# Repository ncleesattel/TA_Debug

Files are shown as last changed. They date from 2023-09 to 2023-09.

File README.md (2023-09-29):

# TA_Debug
PCB designed with KiCad to make a debug main unit for TeenAstro V3 testing.  
I haven't built my own debug platform yet, so I would encourage you to wait for my feedback.  

## internal connectors
The pcb is intended to accommodate:
* TMC5160 for RA, DEC and Focusser
  * the TMC5160 can either be connected via step/dir or SPI 
* 16 MHz oscillators for TMC5160
* NEO-M8n GNSS satellite positioning system
* DS3232 RTC
* power is supplied from a DC jack that splits into
  * VCC for steppers (12 - 24V)
  * 5V for legacy SHC
  * 3.3V for everything else
  * CR32 battery
* power is provided by two Traco DC/DC converters

## external connectors
An MCU like ESP32 or Teensy 4.x can be connected through a ribbon cable to a breadboard.  
There are also connectors for an SHC, stepper motors and encoders.  

## pictures
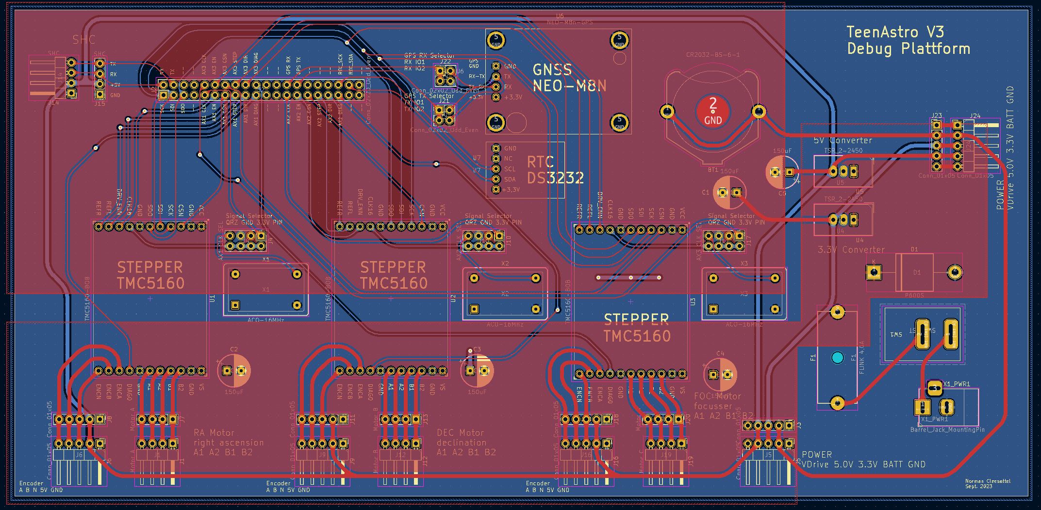
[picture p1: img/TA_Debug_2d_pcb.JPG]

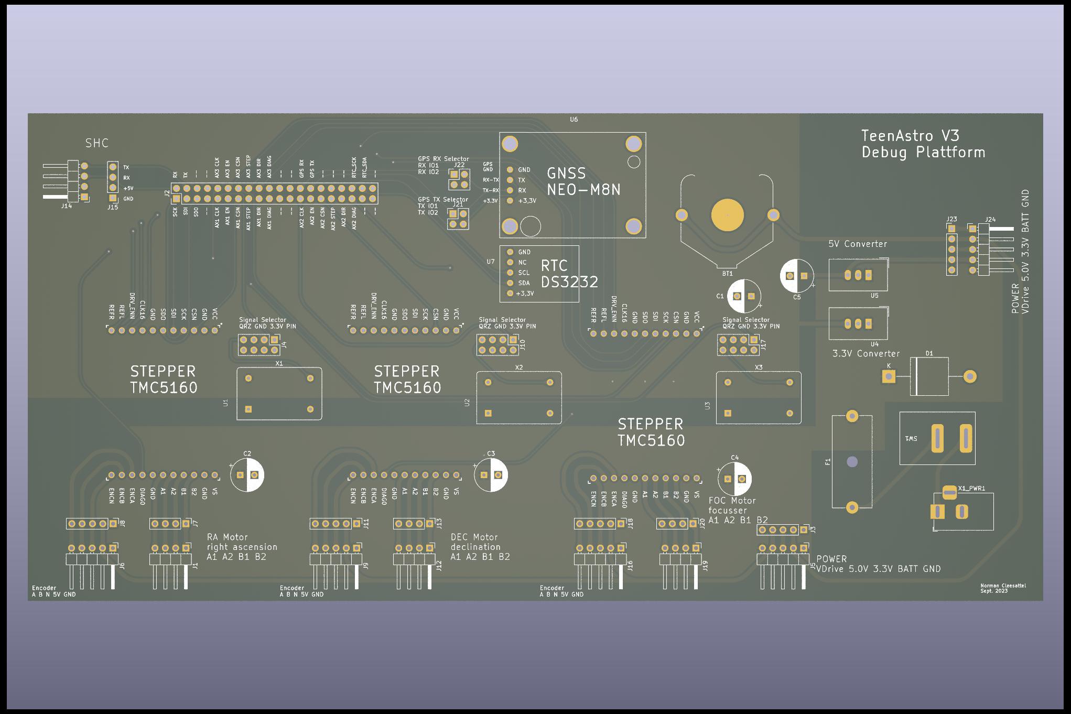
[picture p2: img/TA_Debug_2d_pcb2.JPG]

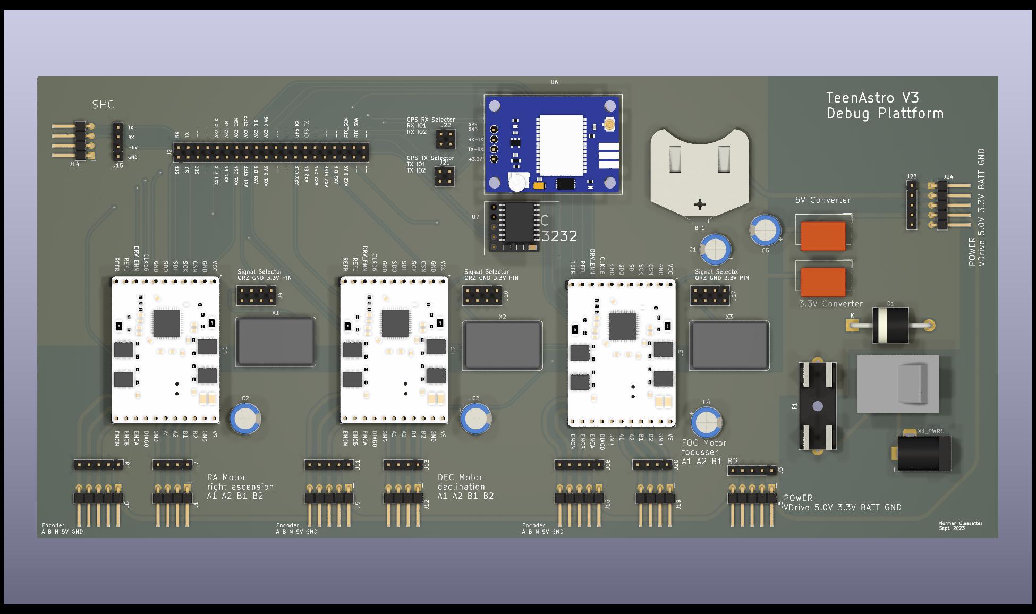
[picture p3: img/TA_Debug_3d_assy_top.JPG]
pcb assy top

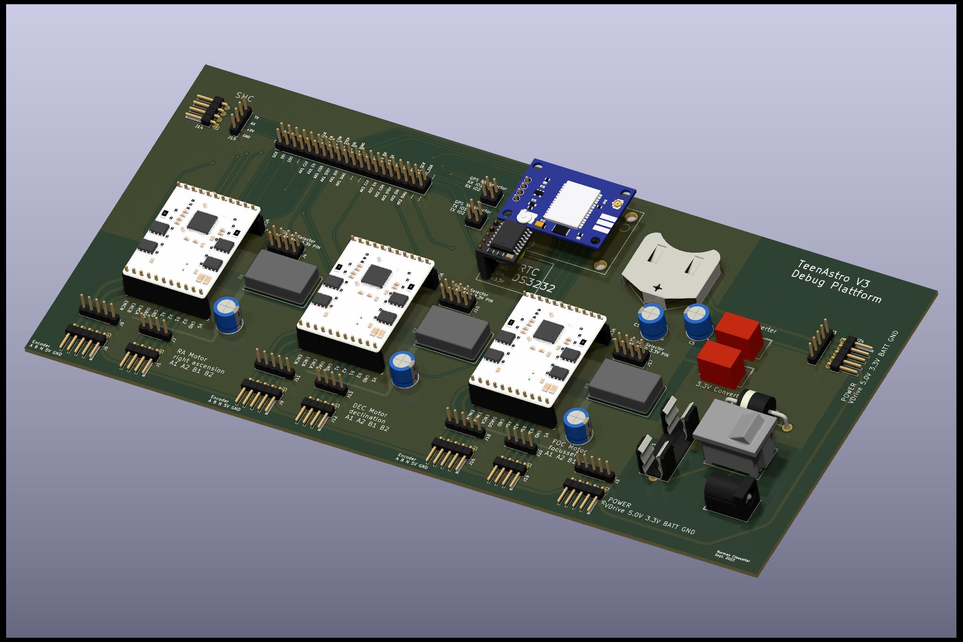
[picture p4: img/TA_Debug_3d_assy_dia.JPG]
pcb assy dia

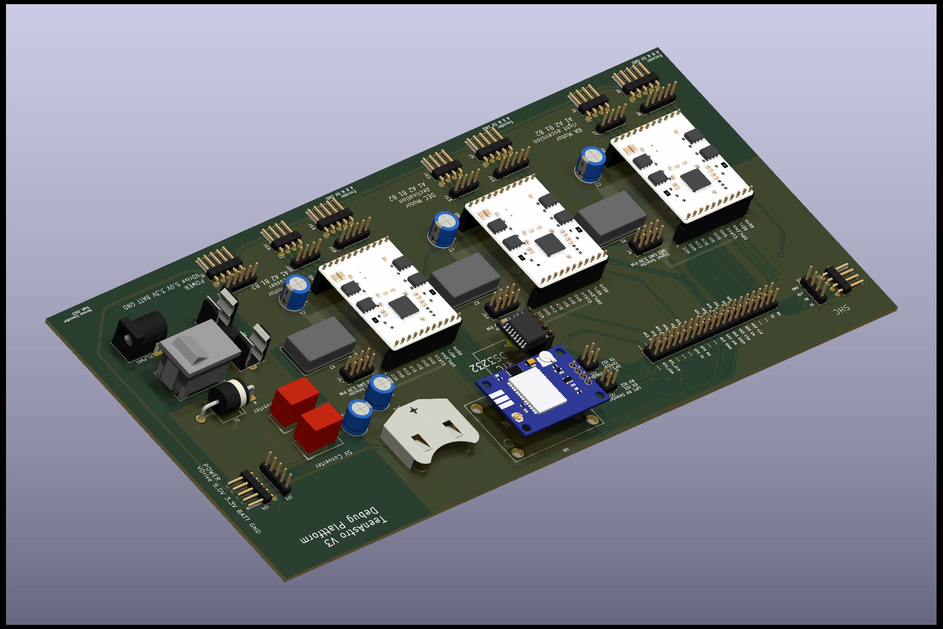
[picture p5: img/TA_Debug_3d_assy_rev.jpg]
pcb assy rev

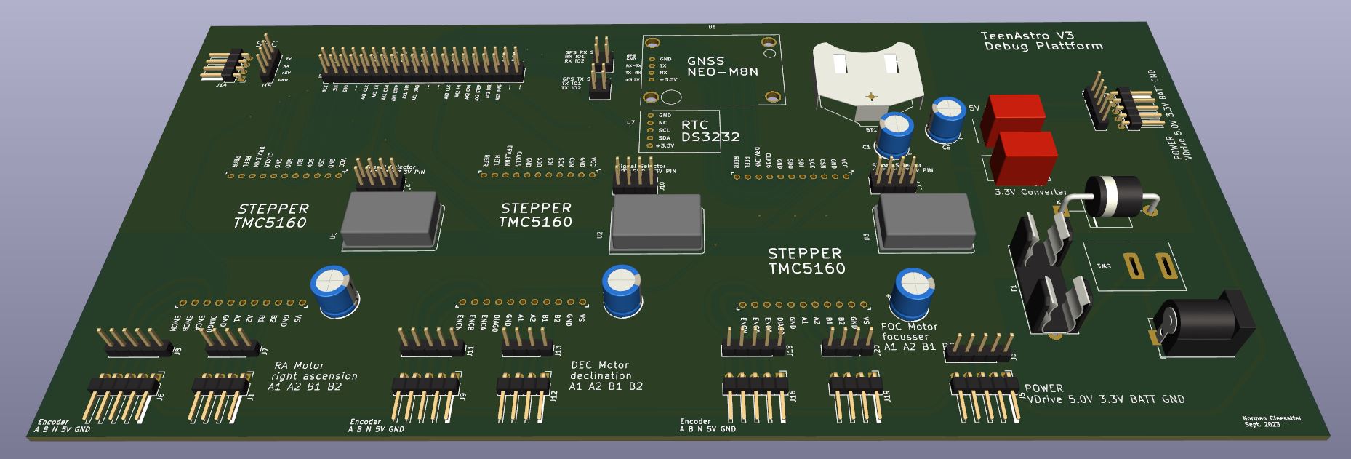
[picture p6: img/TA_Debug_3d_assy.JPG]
pcb assy


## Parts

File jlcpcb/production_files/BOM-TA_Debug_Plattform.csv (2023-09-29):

Comment | Designator | Footprint | LCSC
ACO-16MHz | X3 | Oscillator_DIP-14
TMC5160-BOB | U3 | 22pin1,5x1,1-BOB
Motor C | J20 | PinHeader_1x04_P2.54mm_Vertical
Motor C | J19 | PinHeader_1x04_P2.54mm_Horizontal
Conn_01x05 | J18 | PinHeader_1x05_P2.54mm_Vertical
AX3 CLK SEL | J17 | PinHeader_2x04_P2.54mm_Vertical
Conn_01x05 | J16 | PinHeader_1x05_P2.54mm_Horizontal
SHC | J14 | PinHeader_1x04_P2.54mm_Horizontal
150uF | C4 | CP_Radial_D8.0mm_P3.50mm
150uF | C1 | CP_Radial_D8.0mm_P3.50mm
SW_SPST | SW1 | Marquart
P600S | D1 | D_P600_R-6_P20.00mm_Horizontal
Conn_01x05 | J5 | PinHeader_1x05_P2.54mm_Horizontal
ACO-16MHz | X2 | Oscillator_DIP-14
TSR_2-2450 | U4 | Converter_DCDC_TRACO_TSR-2_THT
Conn_01x05 | J8 | PinHeader_1x05_P2.54mm_Vertical
FLINK 4,0A | F1 | Fuseholder_Cylinder-5x20mm_Schurter_0031_8201_Horizontal_Open
ACO-16MHz | X1 | Oscillator_DIP-14
Conn_01x05 | J11 | PinHeader_1x05_P2.54mm_Vertical
AX1 CLK SEL | J4 | PinHeader_2x04_P2.54mm_Vertical
150uF | C2 | CP_Radial_D8.0mm_P3.50mm
Conn_01x05 | J6 | PinHeader_1x05_P2.54mm_Horizontal
Conn_01x05 | J9 | PinHeader_1x05_P2.54mm_Horizontal
Motor A | J7 | PinHeader_1x04_P2.54mm_Vertical
Barrel_Jack_MountingPin | X1_PWR1 | BarrelJack_Horizontal
TSR_2-2450 | U5 | Converter_DCDC_TRACO_TSR-2_THT
Motor A | J1 | PinHeader_1x04_P2.54mm_Horizontal
Conn_01x05 | J3 | PinHeader_1x05_P2.54mm_Vertical
Motor B | J13 | PinHeader_1x04_P2.54mm_Vertical
Motor B | J12 | PinHeader_1x04_P2.54mm_Horizontal
SHC | J15 | PinHeader_1x04_P2.54mm_Vertical
TMC5160-BOB | U2 | 22pin1,5x1,1-BOB
TMC5160-BOB | U1 | 22pin1,5x1,1-BOB
AX2 CLK SEL | J10 | PinHeader_2x04_P2.54mm_Vertical
150uF | C3 | CP_Radial_D8.0mm_P3.50mm
Conn_02x20_Odd_Even | J2 | PinHeader_2x20_P2.54mm_Vertical
Conn_01x05 | J24 | PinHeader_1x05_P2.54mm_Horizontal
Conn_01x05 | J23 | PinHeader_1x05_P2.54mm_Vertical
CR2032-BS-6-1 | BT1 | Battery_KZH_20P
Conn_02x02_Odd_Even | J22 | PinHeader_2x02_P2.54mm_Vertical
Conn_02x02_Odd_Even | J21 | PinHeader_2x02_P2.54mm_Vertical
NEO-M8n-GPS | U6 | NEO-M8n-GPS
150uF | C5 | CP_Radial_D8.0mm_P3.50mm
~ | U7 | DS3232

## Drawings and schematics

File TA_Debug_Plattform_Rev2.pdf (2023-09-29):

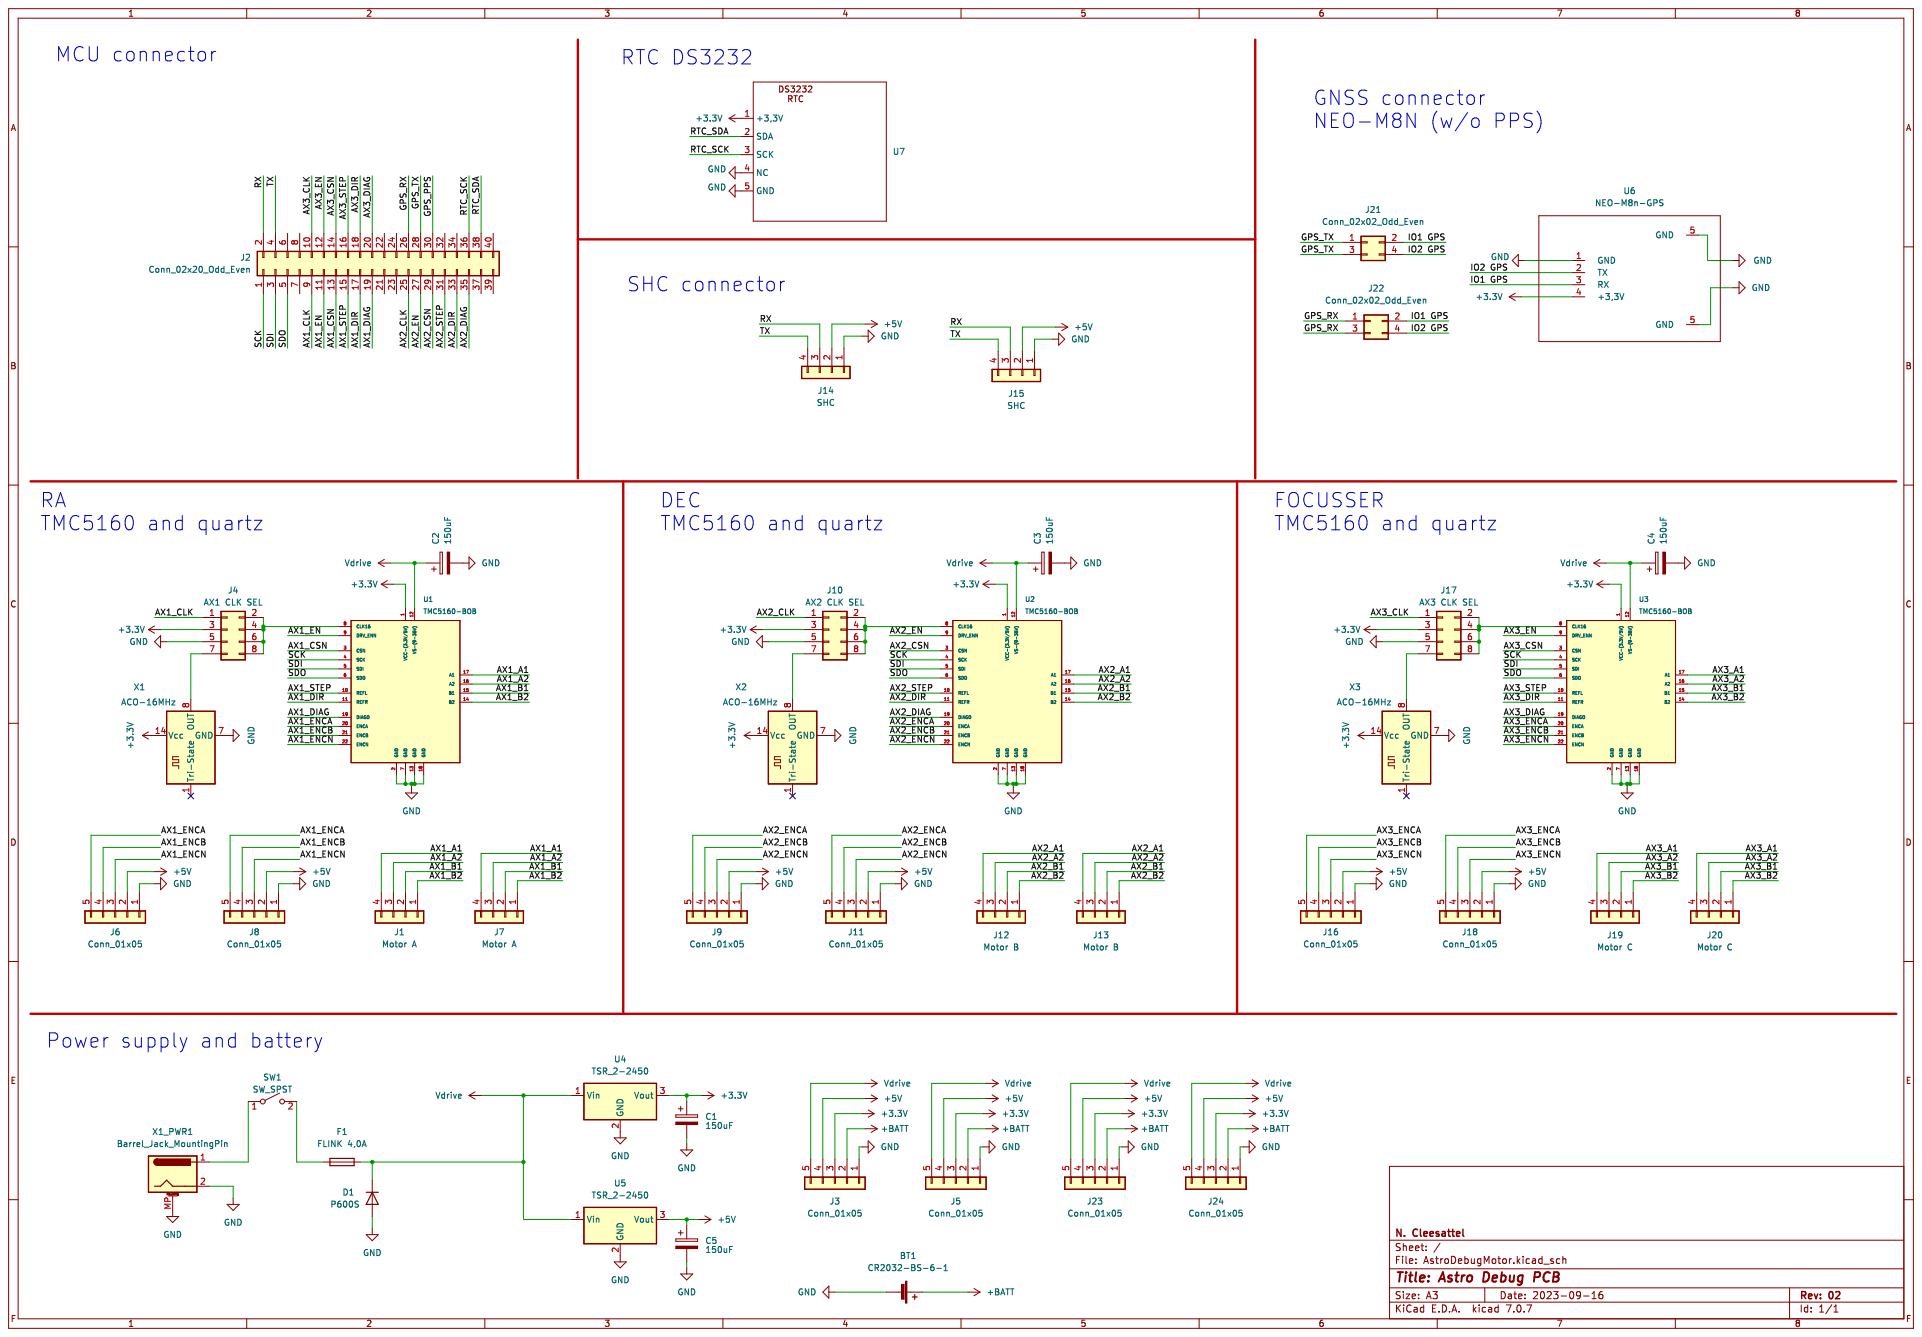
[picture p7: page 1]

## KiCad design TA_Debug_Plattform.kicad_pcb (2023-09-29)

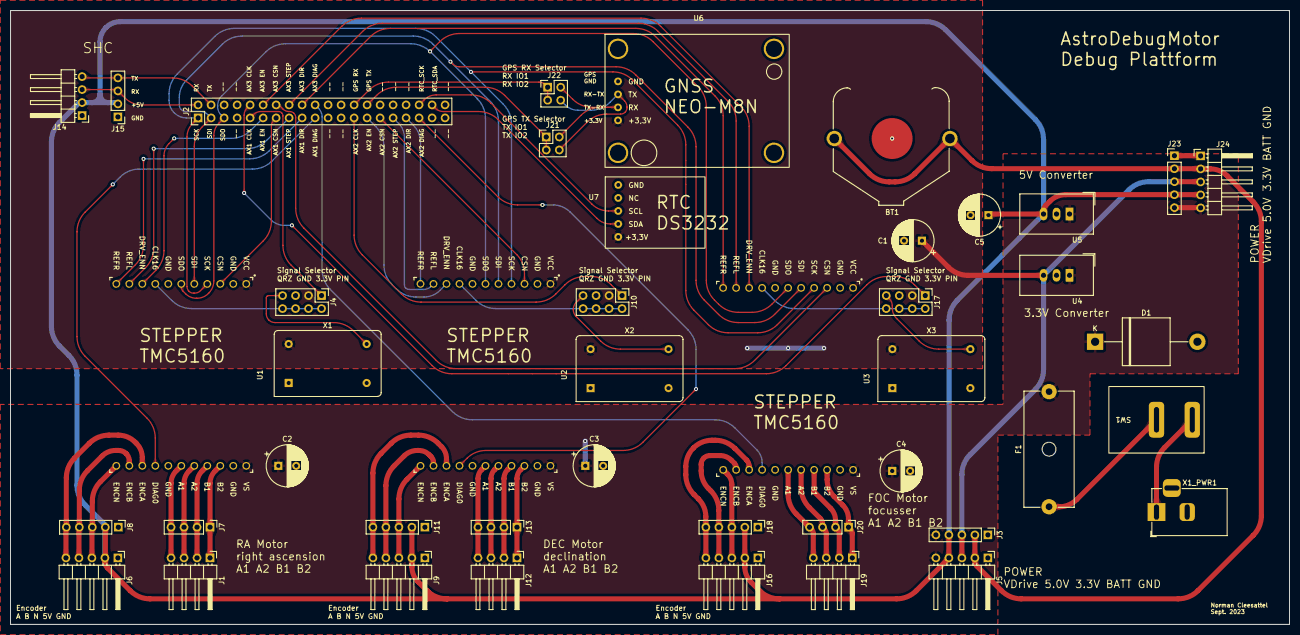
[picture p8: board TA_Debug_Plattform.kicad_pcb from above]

Board: 2 copper layers, 250.0 x 120.0 mm, 44 parts (0 on the bottom side), 63 nets.

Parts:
BT1: CR2032-BS-6-1; Battery_KZH_20P
C1, C2, C3, C4, C5: 150uF; CP_Radial_D8.0mm_P3.50mm
D1: P600S; D_P600_R-6_P20.00mm_Horizontal
F1: FLINK 4,0A; Fuseholder_Cylinder-5x20mm_Schurter_0031_8201_Horizontal_Op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
J1: Motor A; PinHeader_1x04_P2.54mm_Horizontal
J2: Conn_02x20_Odd_Even; PinHeader_2x20_P2.54mm_Vertical
J3, J8, J11, J18, J23: Conn_01x05; PinHeader_1x05_P2.54mm_Vertical
J4: AX1 CLK SEL; PinHeader_2x04_P2.54mm_Vertical
J5, J6, J9, J16, J24: Conn_01x05; PinHeader_1x05_P2.54mm_Horizontal
J7: Motor A; PinHeader_1x04_P2.54mm_Vertical
J10: AX2 CLK SEL; PinHeader_2x04_P2.54mm_Vertical
J12: Motor B; PinHeader_1x04_P2.54mm_Horizontal
J13: Motor B; PinHeader_1x04_P2.54mm_Vertical
J14: SHC; PinHeader_1x04_P2.54mm_Horizontal
J15: SHC; PinHeader_1x04_P2.54mm_Vertical
J17: AX3 CLK SEL; PinHeader_2x04_P2.54mm_Vertical
J19: Motor C; PinHeader_1x04_P2.54mm_Horizontal
J20: Motor C; PinHeader_1x04_P2.54mm_Vertical
J21, J22: Conn_02x02_Odd_Even; PinHeader_2x02_P2.54mm_Vertical
SW1: SW_SPST; Marquart
U1, U2, U3: TMC5160-BOB; 22pin1,5x1,1-BOB
U4, U5: TSR_2-2450; Converter_DCDC_TRACO_TSR-2_THT
U6: NEO-M8n-GPS
U7: DS3232
X1, X2, X3: ACO-16MHz; Oscillator_DIP-14
X1_PWR1: Barrel_Jack_MountingPin; BarrelJack_Horizontal

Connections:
+3.3V: C1.1, J3.3, J4.3, J5.3, J10.3, J17.3, J23.3, J24.3, U1.1 (VCC-(3.3V/5V)), U2.1 (VCC-(3.3V/5V)), U3.1 (VCC-(3.3V/5V)), U4.3 (Vout), U6.4 (+3,3V), U7.1 (+3,3V), X1.14 (Vcc), X2.14 (Vcc), X3.14 (Vcc)
+5V: C5.1, J3.4, J5.4, J6.2, J8.2, J9.2, J11.2, J14.2, J15.2, J16.2, J18.2, J23.4, J24.4, U5.3 (Vout)
+BATT: BT1.1 (+), J3.2, J5.2, J23.2, J24.2
/AX1_A1: J1.4, J7.4, U1.17 (A1)
/AX1_A2: J1.3, J7.3, U1.16 (A2)
/AX1_B1: J1.2, J7.2, U1.15 (B1)
/AX1_B2: J1.1, J7.1, U1.14 (B2)
/AX1_CLK: J2.9, J4.1
/AX1_CSN: J2.13, U1.3 (CSN)
/AX1_DIAG: J2.19, U1.19 (DIAGO)
/AX1_DIR: J2.17, U1.11 (REFR)
/AX1_EN: J2.11, U1.9 (DRV_ENN)
/AX1_ENCA: J6.5, J8.5, U1.20 (ENCA)
/AX1_ENCB: J6.4, J8.4, U1.21 (ENCB)
/AX1_ENCN: J6.3, J8.3, U1.22 (ENCN)
/AX1_STEP: J2.15, U1.10 (REFL)
/AX2_A1: J12.4, J13.4, U2.17 (A1)
/AX2_A2: J12.3, J13.3, U2.16 (A2)
/AX2_B1: J12.2, J13.2, U2.15 (B1)
/AX2_B2: J12.1, J13.1, U2.14 (B2)
/AX2_CLK: J2.25, J10.1
/AX2_CSN: J2.29, U2.3 (CSN)
/AX2_DIAG: J2.35, U2.19 (DIAGO)
/AX2_DIR: J2.33, U2.11 (REFR)
/AX2_EN: J2.27, U2.9 (DRV_ENN)
/AX2_ENCA: J9.5, J11.5, U2.20 (ENCA)
/AX2_ENCB: J9.4, J11.4, U2.21 (ENCB)
/AX2_ENCN: J9.3, J11.3, U2.22 (ENCN)
/AX2_STEP: J2.31, U2.10 (REFL)
/AX3_A1: J19.4, J20.4, U3.17 (A1)
/AX3_A2: J19.3, J20.3, U3.16 (A2)
/AX3_B1: J19.2, J20.2, U3.15 (B1)
/AX3_B2: J19.1, J20.1, U3.14 (B2)
/AX3_CLK: J2.10, J17.1
/AX3_CSN: J2.14, U3.3 (CSN)
/AX3_DIAG: J2.20, U3.19 (DIAGO)
/AX3_DIR: J2.18, U3.11 (REFR)
/AX3_EN: J2.12, U3.9 (DRV_ENN)
/AX3_ENCA: J16.5, J18.5, U3.20 (ENCA)
/AX3_ENCB: J16.4, J18.4, U3.21 (ENCB)
/AX3_ENCN: J16.3, J18.3, U3.22 (ENCN)
/AX3_STEP: J2.16, U3.10 (REFL)
/GPS_RX: J2.26, J22.1, J22.3
/GPS_TX: J2.28, J21.1, J21.3
/IO1 GPS: J21.2, J22.2, U6.3 (RX)
/IO2 GPS: J21.4, J22.4, U6.2 (TX)
/RTC_SCK: J2.36, U7.3 (SCK)
/RTC_SDA: J2.38, U7.2 (SDA)
/RX: J2.2, J14.3, J15.3
/SCK: J2.1, U1.4 (SCK), U2.4 (SCK), U3.4 (SCK)
/SDI: J2.3, U1.5 (SDI), U2.5 (SDI), U3.5 (SDI)
/SDO: J2.5, U1.6 (SDO), U2.6 (SDO), U3.6 (SDO)
/TX: J2.4, J14.4, J15.4
GND: BT1.2 (-), C1.2, C2.2, C3.2, C4.2, C5.2, D1.2 (A), J3.1, J4.5, J5.1, J6.1, J8.1, J9.1, J10.5, J11.1, J14.1, J15.1, J16.1, J17.5, J18.1, J23.1, J24.1, U1.2 (GND), U1.7 (GND), U1.13 (GND), U1.18 (GND), U2.2 (GND), U2.7 (GND), U2.13 (GND), U2.18 (GND), U3.2 (GND), U3.7 (GND), U3.13 (GND), U3.18 (GND), U4.2 (GND), U5.2 (GND), U6.1 (GND), U6.5 (GND), U7.4 (NC), U7.5 (GND), X1.7 (GND), X1_PWR1.2, X2.7 (GND), X3.7 (GND)
unnamed: J4.2, J4.4, J4.6, J4.8, U1.8 (CLK16)
unnamed: J4.7, X1.8 (OUT)
unnamed: J10.2, J10.4, J10.6, J10.8, U2.8 (CLK16)
unnamed: J10.7, X2.8 (OUT)
unnamed: J17.2, J17.4, J17.6, J17.8, U3.8 (CLK16)
unnamed: J17.7, X3.8 (OUT)
unnamed: SW1.1 (A), X1_PWR1.1
unnamed: F1.1, SW1.2 (B)
Vdrive: C2.1, C3.1, C4.1, D1.1 (K), F1.2, J3.5, J5.5, J23.5, J24.5, U1.12 (VS-(9-36V)), U2.12 (VS-(9-36V)), U3.12 (VS-(9-36V)), U4.1 (Vin), U5.1 (Vin)
